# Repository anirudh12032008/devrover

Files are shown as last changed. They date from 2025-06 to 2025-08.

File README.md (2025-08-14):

# Dev Rover by Anirudh

Dev Rover is your personal rover which can move on its own, it has a esp32 with a camera that helps it to idetify things and navigate through the surroundings. it can be controlled by voice commands ( with the help me MAX9814) and can be controlleed by its own web applivation. It also has a speaker which can play some cool sounds. Its also equipped with a tilted 1.3 inc Oled display which can help the developer to see and visualize things. It ill run on 3/6 LiPo battery. It has 4 dc motors controlled by L298N motor driver. It has a 3D printed body which is light weight and durable. It can be used for various purposes like surveillance, exploration, and off course to show off to your friends.

## Why build dev rover?
I always wanted to build a robot like rover, which can move on my voice commands and off course I wanted to show it off to my friends. It will also help me entertain, remind, help while im programming and studying, it can also entertain me with some cool sounds when Im bored. and remind me to drink water and take breakes

## Features
- **Voice Control**: MAX9814 microphone.
- **Camera Navigation**: ESP32 camera for real-time video streaming and object identification.
- **Web Application Control**: Control the rover through web interface.
- **Audio Feedback**: Play sounds through a speaker for alerts and update
- **OLED Display**: 1.3-inch display for feedback and information.
- **Battery Powered**: Runs on a 3/6 LiPo battery 
- **4 DC Motors**: Powered by an L298N motor driver
- **3D Printed Body**: Lightweight and durable design

d1
d2
d3
d4

f4
circuit
p2
p1

f3
f2
f1

# final build
dev

# Youtube Link
https://youtu.be/ks2maEaWWV4?si=1bKzCrpTWsTYReYF

## Bill of Materials
| Component | Price (INR) | Price (USD) |
|---|---|---|
| ESP32 WROOM | 320 | 3.70 |
| TT DC Motor | 308 | 3.56 |
| Battery 3.7V (3-Pack of 2) | 546 | 6.30 |
| ESP32 Camera | 1040 | 12.01 |
| Battery Holder (2x3 cell) | 58 | 0.67 |
| L298D Motor Driver | 78 | 0.90 |
| TP4056 USB-C Charging Module | 32 | 0.37 |
| Switches | 202 | 2.33 |
| SH1106 OLED Display | 220 | 2.54 |
| SD Card Reader | 25 | 0.29 |
| MAX9814 Microphone Module | 166 | 1.92 |
| Speaker 2W 4Ω | 290 | 3.35 |
| PAM8403 Amplifier Module | 51 | 0.59 |
| 10-Segment LED Bar Graph | 70 | 0.81 |
| Buck Converter | 35 | 0.40 |
| WS2812 RGBIC LED Strip | 289 | 3.34 |
| M3 Screws (Pack of 10) | 120 | 1.39 |
| Terminal Block | 48 | 0.55 |
| 3D Case | 870 | 10.00 |
| PCB | 870 | 10.00 |
| Miscellaneous | 435 | 5.00 |
| **Tax** | **296.5** | **3.41** |
| | | |
| **Total** | **₹6369.5** | **$73.42**  |

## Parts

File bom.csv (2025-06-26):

Name | Price(INR) | Price(USD) | Link
ESP32 WROOM | 320 | 3.695150115 | https://ebhoot.in/shop-2/esp-wifi-boards/esp32-development-board-type-c-usb-ch340c-wifi-bluetooth-ultra-low-power-dual-core/
TT DC Motor | 308 | 3.556581986 | https://www.amazon.in/gp/product/B078NYD1MZ/ref=ewc_pr_img_1?smid=AJ6SIZC8YQDZX&psc=1
Battery 3.7V (3xPack of 2) | 546 | 6.304849885 | https://www.importdukan.com/li-ion-18650-3.7v-2600mah-battery-3c?search=battery+3.7
ESP32 Camera | 1040 | 12.00923788 | https://www.amazon.in/ESP32-Module-Bluetooth-OV2640-Camera/dp/B0BRXKNLFG/ref=sr_1_9?sr=8-9
Battery Holder (2x3 cell) | 58 | 0.6697459584 | https://ebhoot.in/shop-2/power-supply/battery-battery-holder/18650-battery-holder-for-lithium-ion-3-cell/
L298D Motor Driver | 78 | 0.9006928406 | https://ebhoot.in/shop-2/electronics-modules/motor-driver-modules/l298-2a-dual-motor-driver-module-with-pwm-control/
TP4056 USB-C Charging Module (x2) | 32 | 0.3695150115 | https://ebhoot.in/shop-2/electronics-modules/bms-module-battery-charging-module/tp4056-1a-li-ion-lithium-battery-charging-module-with-current-protection-type-c/
Switches | 202 | 2.33256351 | https://www.amazon.in/Electronicspices-Switchs-electronic-science-project/dp/B08TRDX6LW?s=industrial
SH1106 Oled | 220 | 2.540415704 | https://ebhoot.in/shop-2/display-devices/1-3-inch-i2c-iic-4-pin-oled-display-module-with-vcc-gnd-blue/
SD card reader | 25 | 0.2886836028 | https://ebhoot.in/shop-2/electronics-modules/interfacing-modules/micro-sd-card-module-breakout-board/
MAX9814 Microphone Module | 166 | 1.916859122 | https://www.importdukan.com/max9814-high-performance-microphone-agc-amplifier-module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
Speaker 2W 4ohm | 290 | 3.348729792 | https://www.amazon.in/Invento-8944638610755-Loudspeaker-Speaker-Replace/dp/B06XFJGV9K
PAM8403 | 51 | 0.5889145497 | https://www.importdukan.com/pam8403-mini-5v-digital-amplifier-board-with-switch-potentiometer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
10 Segment LED Bar Graph | 70 | 0.8083140878 | https://www.amazon.in/cart/smart-wagon?newItems=3d17a9ca-eada-479b-af5a-62ccfd44ab0d,1
Buck Convertor (x2) | 35 | 0.4041570439 | https://ebhoot.in/shop-2/electronics-modules/buck-boost-converters/lm2596-dc-dc-buck-converter-adjustable-step-down-power-supply-module/
WS2812 RGBIC LED Strip | 289 | 3.337182448 | https://www.amazon.in/AURECIS-Individually-Addressable-Non-Waterproof-Combinations/dp/B0F9FRZH69
M3 Screw( pack of 10) | 120 | 1.385681293 | https://www.amazon.in/Rpi-shop-Phillip-Phillips-Quantity/dp/B08FG7DL3T?sp_csd=d2lkZ2V0TmFtZT1zcF9hdGY
Terminal Block | 48 | 0.5542725173 | https://www.importdukan.com/2-pin-5.08mm-pitch-pluggable-screw-terminal-block-connector-blue
3D Case | 870 | 10 | printing legion
Tax | 296.5 | 3.408045977
PCB | 870 | 10 | Rough Estimate
Misc. | 435 | 5
 |  | 0
 |  | 0
Total | 6369.5 | 73.41959332

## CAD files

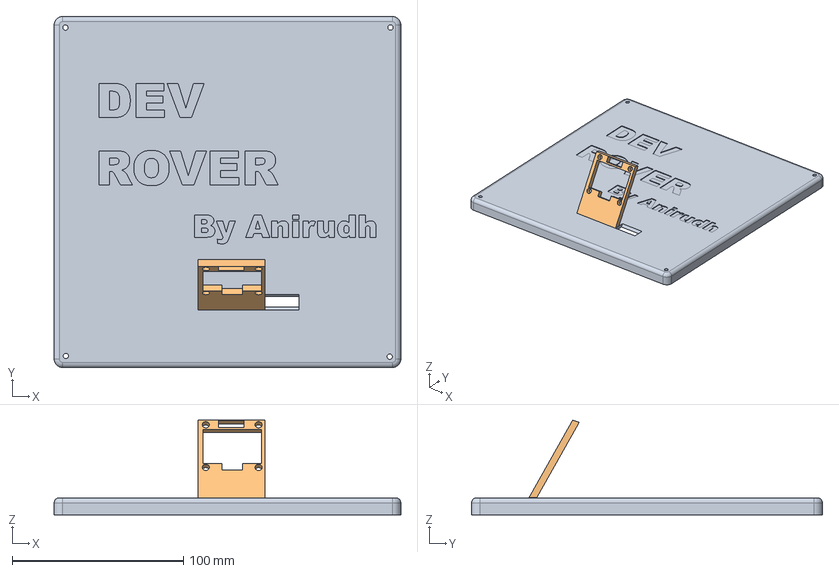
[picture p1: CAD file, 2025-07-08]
cad/top_rover.step
202.5 x 205.0 x 55.4 mm

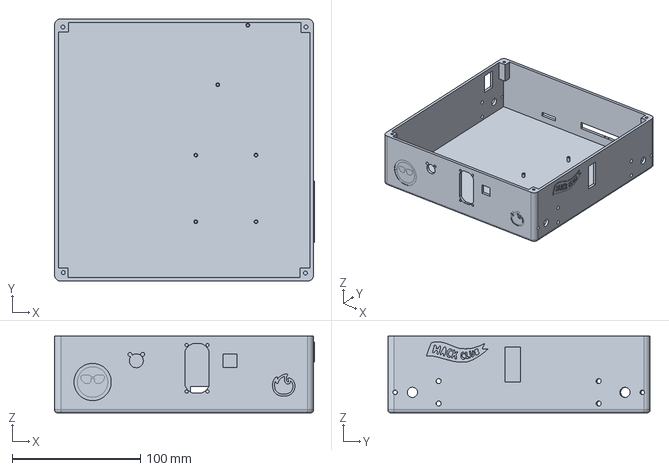
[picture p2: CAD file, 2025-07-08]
cad/Bottom_rover.step
203.1 x 205.0 x 60.0 mm

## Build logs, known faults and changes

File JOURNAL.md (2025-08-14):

# JOURNAL 
Title - " DEV ROVER "
Author - Anirudh Sahu
description - Dev Rover is your personal rover which can move on its own, it has a esp32 with a camera that helps it to idetify things and navigate through the surroundings. it can be controlled by voice commands ( with the help me MAX9814) and can be controlleed by its own web applivation. It also has a speaker which can play some cool sounds. Its also equipped with a tilted 1.3 inc Oled display which can help the developer to see and visualize things. It ill run on 3/6 LiPo battery. It has 4 dc motors controlled by L298N motor driver. It has a 3D printed body which is light weight and durable. It can be used for various purposes like surveillance, exploration, and off course to show off to your friends.
created_at - 2025-06-11
## Total Time - 44 Hr

## June 11th: researched around the topic and created a rough schematic and PCB
3 PM IST - 6:20 PM IST
Initially I started with creating a rough plan of what exactly to include in my project.
As its a smart rover ill need a few dc motor a couple of servo motors and a mini computer to make it smart.
So as this is my starting project I didnt really knew how to get started with the PCB designing. i used Easy EDA but still when I seareched for components There were wayy tooo many options so I was overwhelmed and confused then I selected a esp32 and a L298N I have a knowledge of physical components just the firmware is new then I made the intial connections with the esp32 but later I found that the ESP32 I was using didnt had a 5V power supply so I had to restart and find a new one which took a bit time and also I had to understand why this happened. next I created a rough pcb and a 3d view of it I'm now planning to try some other alternatives for the designing part. 



Total time spend 3 hr

## June 12th: Started with designing the case
6 pm ist to 10 pm ist
These were one of the worst hours in my journey. I started with the recommendations from others to use onshape but when I actually started I had a really hard time. first the models I imported had 300 parts so to move it to the center I had to select all which made my computer burst lol ( not literally ) then I learned about onshape it had very less tutorials also so still I managed but then again it started to lag too much. I literally couldnt think of anything else then I asked in slack so I'll start my journey with most probable fusion360 from tommorow. Todays day made me learn many things and I also have models of esp32, servo motor, dc motor, l298 motor Driver

 
Total time spend : 4 hr

## Jun 13: Continue Designing the case
4 PM IST to 7:45 PM IST
So I started with downloading Fusion 360, Its definitely better then Onshape, so I knew what exactly I wanted to get started on took some time to get familier to the software then got started with the actual work, imported to models took some more time then started to create a sketch and then a plane then a surface and excruded it to make a base. wwasnt sure with the dimensions so researched online to find the right dimensions. ill continue tomorrow with the case and planning to move to the electriv circuits next

Total time spend : 3.75 Hr

## Jun 14: Continue with the planning and the 3D case
6:30 PM IST to 11:30 PM IST
Continued developing the model. Had some issue regarding how would the actual model look like but after exploring other ideas and designs I planned to make it in like a Box thats like a perfect robo shape lol, so I first researched for the components that ill be using and found there 3d models to import, due to budget constraint I droppeed the servo motors for the pickup thing. But I added the the mother components. Created the sketches for each model and had my case in 2 parts for top and bottom also added the screen. Took some time to seaerch online on how to do a thing but now I am familiar with the overall software so from today things will go on more fast!!! 





Total Time Spend : 4 Hr

## June 15: Changed the components and layout
7:15 PM IST to 11 PM IST
So today I continued with the case but then after reconsideration I reselected the components required, I replaced the 0.93 inch oled with 1.3 one and added other components like a speaker and a microphone to receive audio input and I also changed the overall layout so I removed the previous bodies and components and added the new also this time I kept in mind about where exactly each component will be in the final design. Now I have included all the models that I will be using in the final rover. I made sure that the 3D model that I was using is available on Amazon or other places and have the right dimensions so that I don't face any issue later. Some models weren't available on grabcad so I surfed the web for it. 




Total Time Spend: 3.75 Hr

## June 16: Designed the 3d structure especially for oled
I started with creating the base structure. firstly created the sketches for all components.then I worked for the oled display structure. It took a bit time but atleast I can see things turning into the model. Tommorow I'll try to complete the structure for all of the components.





Total time Spent: 3hr

## June 17: Designed most of the model
Continuing the work that I did yesterday, took a bit long because first my sketch pallete disappeared asked for help but didnt found any solution both on internet and slack. Still I continued with the designing first I finished the bottom then insted of procastination I finished all sides also and added holes where ever needed, added a few holes on the base for esp and l298




Total Time Spent: 4.5 Hr

## June 19: Completed the 3D model
Finished completing the 3D model, added the holes and improved some small details by taking feedbacks on slack. I will be using rgb strip around it so left a small hole near the oled stand to let the wires in


Total Time Spent: 2 Hr

## June 20: Finished the Case and created the BOM 
added a hole for the Camera, while creating the BOM I also noticed that the esp32 was having wrong holes so fixed it also improved the holes and fixed minor issues on the suggestions from others. Creating the BOM was the most important part, for India i couldn't find any website which had all the parts so at last i used Amazon. then the issue was there were many parts which had shipping cost more then the actual part cost. some had the minimum order quantity requirements. But Overall I got everything in 80-85$ which is quite good as of what I had thought initially.
Time Spent : 3 Hr

## June 21: Completed the code for the rover to move 
Added a web server for the rover to communicate with and implemented the logics to move
r1
Time Spent : 2.5 Hr

## June 22: Completed the full Project
Implemented all the features in the code so that I have full code available when then hardware arrives, added the remaining parts. Researched about some small details that I could improve in the overall project.
Written the Readme for the Project. Added some cool details in the 3D model. Created the Circuit diagram
f7
f6
f5
circuit
f4
f3
f2
f1

Time Spent - 6Hr ( including 1AM 23th)

## June 25: Created PCB
As Cyao told me to create a PCB I started creating the PCB, making it a big pcb would just increase its price so I tried to keep it compact. I initally started with creating my own motor driver but then when I checked the price for PCBA it was more then 5x a module so I decided to use only hand soldered items to save money on the PCB and create the pcb to make things clutter free.
p2
p1
Time Spent - 3.5 hr

## July 9-10: Started building physically 
recived all the parts so I started to build the main project. couldn't get the 3d print so I planned to work on a wooden base for prototype. integrated the camera and also completed the working rover. it can move right now the main issue was that Arduino IDE sucks adn the esp32 am was getting too hot
Screenshot_2025-07-11-08-56-51-107_com android chrome
Screenshot_2025-07-11-08-57-54-085_com gallery player
Screenshot_2025-07-11-08-58-22-102_com gallery player


## Day 12 
So now I added the PAM amplifier and speaker but the issue was I couldn't play anything so then  headed to
Install the sd card module with it I did everything but still it was not working
Then I thought maybe it's some issue with my SD Card so I tried 3 more cards and formatted them and tried again but still it wasn't working but then U realised that how fool I am I was powering it with 3.3V when it should have been powered by 5V after doing that yess it started working
So I setup that and yeah the audio system was working but was having very very very bad quality but I found some more code online to take reference and then after some long tine taking compiling I made something working, I haven't been able to get a perfect audio but it is pretty good quality now
photo_6102760546496530531_w
photo_6102760546496530527_w
time - 7hr

## Day 13
Added the camera to the main esp32. I streammed the espcam on its own server and then used it with the main Esp32 I also added a new endpoint to control the flash value then I changed the main Esp32 code to connect with the espcam server and show the data I also added slider so that I can control the led but then I realised I should also add some way to control the quality so I added another slider to control the quality of the feed. Now the main issue coming is that the espcam is shutting down after like 1-2 minutes!
So, today I solved the ESP32 camera problem by finding a capacitor as I didn't have a capacitor in my BOM, but I really needed it. So I went to a shop and I asked ChatGPT which one to get. So he suggested me to get a 470 MUF or 1000 MUF. So, I went there and I preferred 1000 MUF because the bigger it is, the better it is. Like in the value-wise and it's a pretty big one. Around 35 volts, so yeah. After using that and I also got a 470 MUF for the main ESP32 also. Because it told me that it would avoid the voltage spikes. Still the esp cam had the same issue
So, still it wasn't working, so I need to diagnose the main issue. To be honest, I couldn't find anything which was doing it. So I went to the internet, I searched for a few things, and then I got a Reddit thread that some user faced the same issue but with some other module, because I was fool, I was covering it with the L298 motor driver's 5V, which is 2-2 unstable. Because whenever the car moves, the voltage drops, and the ESP cam is like a current sucker, so it do need a lot of current, I guess around 500 or 600 ampere. So yeah, I used a buck converter to drop the voltage from the 3 battery pack from 12V to 5V, and used it for the power supply, and it works pretty well now.

photo_6102760546496530523_w

time - 8hr

## Day 14
So now I got into another trouble that the camera and the main ESP shut down like whenever the motor started running. So it was pretty strange because yesterday it was working pretty fine. So I did some recompiling and some more testing. Externally I tested it but everything was working so I didn't know what issue came. So then I took out my voltmeter and multimeter and then when I placed it on the battery pack I came to know that the batteries are discharged. It's not 12V now it's around 7V due to which the L298 drives too much power and the ESP just shut down. So I had another issue that how would I charge the batteries. So I had no option to actually charge the batteries as I got a TP4056 but it was a 3S battery pack. So how would I even charge it. So this was a design flaw from my side. And I searched online for some of the things that could do the job but I couldn't find anything. So what I did is I just had a couple of TP4056 from the local store and some battery holders. And I have a lot of chargers at my home so I just plugged every 3 battery cell into different battery holders and charged them individually. And after that it was working really great. So yeah that was a really nightmare situation.
photo_6102760546496530516_w
time - 2hr

## Day 15
So, today I received my PCB and when I saw the PCB, the obvious flaw that I came to notice is that I was having the wrong MCU. I was having the ESP32 with 30 pins but in the PCB it was of 38 pins and I was really screwed up because I couldn't really return it as I just opened packet of ESP32. So, yeah, I was in a really doubtful situation but I had only one choice. I first searched the internet to find any relevant resources but I couldn't find any. So, my next attempt was to manually fix this design flaw.
photo_6102760546496530536_w
time - 3hr

## Day 16 
I added everything that was left added the rgb strip, the led graph, added the eyes to the oled this was really tough because of obvious reasons that it was for that shitty 0.96 oled all the libraries so I needed to make my own for the 1.3 so It was really exhaustive learning about stuff asking gemini but finally I managed to get it done
I also improved the overall UI of the web interfce because it was pretty shitty before 
photo_6102760546496530561_w
photo_6102760546496530560_w
photo_6102760546496530559_w

time - 4hr

## Day 17
So I started doing the final build and I;m really really tired now  it was very messy everything started to stop working and then start working so I knew I am fucked up but I dont really have words for what happened it just did happened but somehow I did it and im dead now lol
photo_6120626171633846730_w
photo_6120626171633846731_w
photo_6120626171633846732_w
photo_6120626171633846733_w
photo_6120626171633846734_w
dev

time - 3hr

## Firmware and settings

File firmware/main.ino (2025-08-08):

#include <WiFi.h>
#include <AsyncTCP.h>
#include <ESPAsyncWebServer.h>
#include <SD.h>
#include <SPI.h>
#include <U8g2lib.h>
#include <Wire.h>
#include <Adafruit_NeoPixel.h>

// Use a different GPIO pin since 23 is for the SD card
#define LED_PIN    2 // Data pin for the NeoPixel strip
#define NUM_LEDS   60 // Number of LEDs in your 1-meter strip

Adafruit_NeoPixel strip(NUM_LEDS, LED_PIN, NEO_GRB + NEO_KHZ800);

File audioFile;
bool isPlaying = false;
#define SD_CS 5

// ====== WiFi Config ======
const char* ssid = "Dev Bhai OP";
const char* password = "devbhai123omsairam";
const char* ap_ssid = "ESP32-Rover-AP";
const char* ap_password = "robotpassword";
// ====== Motor Pins ======
const int IN1 = 26, IN2 = 27, IN3 = 14, IN4 = 12, ENA = 13, ENB = 33;

// ====== Speaker & Mic Config ======
const int speakerPin = 25;  // DAC1 -> PAM8403
const int micPin = 34;
int threshold = 1940;
unsigned long lastTriggerTime = 0;
unsigned long debounceDelay = 100;
int micValue = 0;
bool soundDetected = false;

#define SCREEN_WIDTH 128
#define SCREEN_HEIGHT 64
#define OLED_RESET -1
#define SCREEN_ADDRESS 0x3C

U8G2_SH1106_128X64_NONAME_F_HW_I2C u8g2(U8G2_R0, /* reset=*/ U8X8_PIN_NONE);

// ====== Globals ======
int currentSpeed = 150;
String currentDir = "stop";
AsyncWebServer server(80);

// Eye state variables (simplified)
int left_eye_x_pos = 0;
int left_eye_y_pos = 0;
int right_eye_x_pos = 0;
int right_eye_y_pos = 0;
const int eye_size = 40;
const int eye_spacing = 10;
const int corner_radius = 10;
const int eye_offset = 10; // Offset for movements



void draw_eyes() {
  u8g2.clearBuffer();
  u8g2.drawRBox(left_eye_x_pos, left_eye_y_pos, eye_size, eye_size, corner_radius);
  u8g2.drawRBox(right_eye_x_pos, right_eye_y_pos, eye_size, eye_size, corner_radius);
  u8g2.sendBuffer();
}

void center_eyes() {
  left_eye_x_pos = (SCREEN_WIDTH - (eye_size * 2 + eye_spacing)) / 2;
  left_eye_y_pos = (SCREEN_HEIGHT - eye_size) / 2;
  right_eye_x_pos = left_eye_x_pos + eye_size + eye_spacing;
  right_eye_y_pos = left_eye_y_pos;
  draw_eyes();
}

// ====== Tone Functions (unchanged) ======
void smoothBeep(int freq, int durationMs) {
  const int samplesPerCycle = 30;
  float step = 2 * 3.14159 / samplesPerCycle;
  unsigned long endTime = millis() + durationMs;
  while (millis() < endTime) {
    for (int i = 0; i < samplesPerCycle; i++) {
      float wave = sin(i * step);
      int val = 128 + int(wave * 100);
      dacWrite(speakerPin, val);
      delayMicroseconds(1000000 / (freq * samplesPerCycle));
    }
  }
}

void gap(int ms = 100) {
  dacWrite(speakerPin, 0);
  delay(ms);
}

void sayHello() {
  smoothBeep(500, 120); gap(80);
  smoothBeep(460, 100); gap(80);
  smoothBeep(420, 100); gap(80);
  smoothBeep(600, 150); gap(200);
}

void sayWorld() {
  smoothBeep(300, 120); gap(60);
  smoothBeep(360, 100); gap(60);
  smoothBeep(400, 100); gap(60);
  smoothBeep(440, 100); gap(60);
  smoothBeep(480, 120); gap(200);
}

void playWav(const char* filename) {
  if (isPlaying) return;
  audioFile = SD.open(filename);
  if (!audioFile) {
    Serial.println("❌ Cannot open WAV file!");
    return;
  }
  isPlaying = true;
  uint8_t buffer[1];
  for (int i = 0; i < 44; i++) audioFile.read();
  while (audioFile.available() && isPlaying) {
    audioFile.read(buffer, 1);
    dacWrite(speakerPin, buffer[0]);
    delayMicroseconds(125);
  }
  audioFile.close();
  isPlaying = false;
  dacWrite(speakerPin, 0);
}

void stopPlayback() {
  if (isPlaying) {
    isPlaying = false;
    if (audioFile) audioFile.close();
    dacWrite(speakerPin, 0);
  }
}

// ====== Motor Movement and Eye Control ======
void moveCar(String dir, int speed) {
  currentDir = dir;
  currentSpeed = map(speed, 0, 100, 0, 255);

  digitalWrite(IN1, dir == "forward" || dir == "right");
  digitalWrite(IN2, dir == "backward" || dir == "left");
  digitalWrite(IN3, dir == "forward" || dir == "left");
  digitalWrite(IN4, dir == "backward" || dir == "right");

  if (dir == "stop") {
    digitalWrite(IN1, LOW); digitalWrite(IN2, LOW);
    digitalWrite(IN3, LOW); digitalWrite(IN4, LOW);
    center_eyes();
  } else if (dir == "forward") {
    center_eyes();
  } else if (dir == "backward") {
    int centerX = (SCREEN_WIDTH - (eye_size * 2 + eye_spacing)) / 2;
    int centerY = (SCREEN_HEIGHT - eye_size) / 2;
    left_eye_x_pos = centerX;
    left_eye_y_pos = centerY + eye_offset;
    right_eye_x_pos = centerX + eye_size + eye_spacing;
    right_eye_y_pos = centerY + eye_offset;
    draw_eyes();
  } else if (dir == "left") {
    int centerX = (SCREEN_WIDTH - (eye_size * 2 + eye_spacing)) / 2;
    int centerY = (SCREEN_HEIGHT - eye_size) / 2;
    left_eye_x_pos = centerX - eye_offset;
    left_eye_y_pos = centerY;
    right_eye_x_pos = centerX + eye_size + eye_spacing - eye_offset;
    right_eye_y_pos = centerY;
    draw_eyes();
  } else if (dir == "right") {
    int centerX = (SCREEN_WIDTH - (eye_size * 2 + eye_spacing)) / 2;
    int centerY = (SCREEN_HEIGHT - eye_size) / 2;
    left_eye_x_pos = centerX + eye_offset;
    left_eye_y_pos = centerY;
    right_eye_x_pos = centerX + eye_size + eye_spacing + eye_offset;
    right_eye_y_pos = centerY;
    draw_eyes();
  }

  analogWrite(ENA, currentSpeed);
  analogWrite(ENB, currentSpeed);
}

void setupAP() {
  Serial.println("❌ WiFi failed, starting Access Point.");
  WiFi.softAP(ap_ssid, ap_password);
  IPAddress apIP = WiFi.softAPIP();
  Serial.print("✅ AP IP address: ");
  Serial.println(apIP);

  // You may want to display this info on the OLED
  // u8g2.clearBuffer();
  // u8g2.setFont(u8g2_font_6x10_tf);
  // u8g2.drawStr(0, 10, "AP Mode Active");
  // u8g2.drawStr(0, 25, "SSID:");
  // u8g2.drawStr(40, 25, ap_ssid);
  // u8g2.drawStr(0, 40, "Password:");
  // u8g2.drawStr(60, 40, ap_password);
  // u8g2.sendBuffer();
}

void setup() {
  Serial.begin(115200);
  pinMode(IN1, OUTPUT); pinMode(IN2, OUTPUT);
  pinMode(IN3, OUTPUT); pinMode(IN4, OUTPUT);
  pinMode(ENA, OUTPUT); pinMode(ENB, OUTPUT);
  dacWrite(speakerPin, 0);

  u8g2.begin();
  u8g2.setDrawColor(1);
  center_eyes();
  strip.begin();
  strip.show();

  // ====== Wi-Fi Connection Logic with Fallback ======
  Serial.print("Connecting to WiFi...");
  WiFi.begin(ssid, password);

  unsigned long wifiConnectStartTime = millis();
  while (WiFi.status() != WL_CONNECTED && millis() - wifiConnectStartTime < 10000) { // 10 second timeout
    delay(500);
    Serial.print(".");
    center_eyes(); // Animate eyes while trying to connect
  }

  if (WiFi.status() == WL_CONNECTED) {
    Serial.println("\n✅ WiFi Connected!");
    Serial.print("IP Address: ");
    Serial.println(WiFi.localIP());
  } else {
    setupAP(); // Fallback to Access Point if connection fails
  }

  // ... (rest of your setup code remains the same)
  SPI.begin(18, 19, 23, SD_CS);
  if (!SD.begin(SD_CS, SPI)) {
    Serial.println("❌ SD card failed!");
  } else {
    Serial.println("✅ SD card initialized!");
  }

  server.on("/control", HTTP_GET, [](AsyncWebServerRequest *request){
    String dir = request->getParam("dir")->value();
    int speed = request->getParam("speed")->value().toInt();
    moveCar(dir, speed);
    request->send(200, "text/plain", "OK");
  });

  server.on("/say", HTTP_GET, [](AsyncWebServerRequest *request){
    String word = request->getParam("word")->value();
    if (word == "hello") sayHello();
    else if (word == "world") sayWorld();
    else if (word == "startup") { sayHello(); sayWorld(); }
    request->send(200, "text/plain", "Sound Played");
  });

  server.on("/play", HTTP_GET, [](AsyncWebServerRequest *request) {
    if (request->hasParam("track")) {
      String name = request->getParam("track")->value();
      if (name == "test1") playWav("/test1.wav");
      else if (name == "test2") playWav("/test2.wav");
      request->send(200, "text/plain", "Playing " + name);
    } else {
      request->send(400, "text/plain", "No track specified");
    }
  });

  server.on("/stop", HTTP_GET, [](AsyncWebServerRequest *request) {
    stopPlayback();
    request->send(200, "text/plain", "Stopped");
  });

  server.on("/mic", HTTP_GET, [](AsyncWebServerRequest *request){
    String json = "{\"value\":" + String(micValue) + ",\"status\":\"" +
                  (soundDetected ? "Sound Detected!" : "Silent") + "\"}";
    request->send(200, "application/json", json);
  });

  server.on("/", HTTP_GET, [](AsyncWebServerRequest *request){
    String html = R"rawliteral(
<!DOCTYPE html>
<html lang="en">
<head>
    <meta charset="UTF-8">
    <meta name="viewport" content="width=device-width, initial-scale=1.0">
    <title>Dev Rover Control</title>
    <style>
        /* A slightly modified version of Tailwind CSS for a dark theme */
        body {
            font-family: ui-sans-serif, system-ui, -apple-system, BlinkMacSystemFont, "Segoe UI", Roboto, "Helvetica Neue", Arial, "Noto Sans", sans-serif;
            background-color: #1a202c; /* dark gray */
            color: #e2e8f0; /* light gray */
            padding: 1rem;
        }
        h1 {
            color: #ecc94b; /* yellow */
            font-size: 1.875rem; /* 30px */
            line-height: 2.25rem; /* 36px */
            text-align: center;
            margin-bottom: 2rem;
        }
        h2 {
            font-size: 1.5rem; /* 24px */
            line-height: 2rem; /* 32px */
            margin-top: 1.5rem;
            margin-bottom: 0.5rem;
            color: #a0aec0;
            text-align: center;
        }
        .container {
            max-width: 42rem; /* 672px */
            margin-left: auto;
            margin-right: auto;
            display: flex;
            flex-direction: column;
            gap: 1.5rem;
        }
        .grid {
            display: grid;
            grid-template-columns: repeat(2, minmax(0, 1fr));
            gap: 0.5rem;
        }
        .grid-full {
            display: grid;
            grid-template-columns: 1fr;
            gap: 0.5rem;
        }
        @media (min-width: 640px) {
            .grid {
                grid-template-columns: repeat(3, minmax(0, 1fr));
            }
        }
        button {
            display: flex;
            justify-content: center;
            align-items: center;
            padding: 1rem 1.25rem;
            border-radius: 0.5rem;
            font-weight: 600;
            font-size: 1rem;
            line-height: 1.5rem;
            color: #1a202c;
            background-color: #ecc94b;
            border: none;
            cursor: pointer;
            transition-property: background-color;
            transition-duration: 150ms;
        }
        button:active {
            background-color: #d69e2e; /* dark yellow on press */
        }
        .slider-container {
            width: 100%;
            display: flex;
            flex-direction: column;
            align-items: center;
            margin: 1rem 0;
            background-color: #2d3748;
            padding: 1rem;
            border-radius: 0.5rem;
        }
        .slider-container label {
            font-size: 1rem;
            line-height: 1.5rem;
            margin-bottom: 0.5rem;
        }
        .slider-container input[type="range"] {
            width: 90%;
            -webkit-appearance: none;
            height: 0.5rem;
            border-radius: 9999px;
            background: #4a5568;
            outline: none;
            transition: opacity 0.2s;
        }
        .slider-container input[type="range"]::-webkit-slider-thumb {
            -webkit-appearance: none;
            appearance: none;
            width: 1.25rem;
            height: 1.25rem;
            border-radius: 9999px;
            background: #ecc94b;
            cursor: pointer;
        }
        .mic-box {
            background-color: #2d3748; /* gray */
            padding: 1rem;
            border-radius: 0.5rem;
            margin-top: 1rem;
        }
        .mic-box p {
            margin: 0;
            font-size: 1rem;
            line-height: 1.5rem;
            text-align: left;
        }
        .mic-box .status-text {
            color: #68d391; /* green */
        }
    </style>
</head>
<body>
    <div class="container">
        <h1>🚗 Dev Rover Control</h1>
        
        <h2>📷 Live Camera</h2>
        <img src="http://192.168.29.222:81/stream" style="width:100%; border-radius:10px; margin-bottom:10px;">
        
        <div class="slider-container">
            <label for="flashSlider">Flash Brightness: <span id="flashVal">0</span></label>
            <input type="range" min="0" max="255" value="0" id="flashSlider" oninput="updateFlash(this.value)">
        </div>
        <div class="slider-container">
            <label for="resSlider">📷 Resolution: <span id="resLabel">Medium</span></label>
            <input type="range" id="resSlider" min="2" max="10" step="1" value="6" oninput="changeRes(this.value)">
        </div>
        
        <div class="grid">
            <button onmousedown="send('forward',100)" onmouseup="send('stop',0)" ontouchstart="send('forward',100)" ontouchend="send('stop',0)">Forward</button>
            <button onmousedown="send('backward',100)" onmouseup="send('stop',0)" ontouchstart="send('backward',100)" ontouchend="send('stop',0)">Backward</button>
            <button onmousedown="send('left',100)" onmouseup="send('stop',0)" ontouchstart="send('left',100)" ontouchend="send('stop',0)">Left</button>
            <button onmousedown="send('right',100)" onmouseup="send('stop',0)" ontouchstart="send('right',100)" ontouchend="send('stop',0)">Right</button>
            <button class="grid-full" onclick="send('stop',0)">Stop</button>
        </div>
        <div class="slider-container">
            <label for="spd">Speed: <span id="speedVal">50</span>%</label>
            <input type="range" min="0" max="100" value="50" id="spd" oninput="sendSpeed(this.value)">
        </div>
        <div class="grid">
            <button onclick="fetch('/play?track=test1')">▶️ Play test1.wav</button>
            <button onclick="fetch('/play?track=test2')">▶️ Play test2.wav</button>
            <button onclick="fetch('/stop')">⏹️ Stop</button>
        </div>
        <div class="mic-box">
            <h2>🎤 Mic Monitor</h2>
            <p>Value: <span id="micVal">---</span></p>
            <p>Status: <span id="micStatus" class="status-text">Loading...</span></p>
        </div>
    </div>
    <script>
        function updateFlash(val) {
            document.getElementById("flashVal").textContent = val;
            fetch("http://192.168.29.222/flash?level=" + val);
        }
        function changeRes(val) {
            const labels = {
                2: "Ultra High",
                3: "Very High",
                4: "High",
                6: "Medium",
                8: "Low",
                9: "Very Low",
                10: "Ultra Low"
            };
            document.getElementById("resLabel").textContent = labels[val] || "Custom";
            fetch("http://192.168.29.222/control?var=framesize&val=" + val).then(() => console.log("Resolution changed to", val));
        }
        let currentDir = 'stop';
        function send(dir, speed) {
            currentDir = dir;
            fetch(`/control?dir=${dir}&speed=${speed}`);
        }
        function sendSpeed(val) {
            document.getElementById("speedVal").textContent = val;
            fetch(`/control?dir=${currentDir}&speed=${val}`);
        }
        setInterval(() => {
            fetch('/mic')
                .then(res => res.json())
                .then(data => {
                    document.getElementById("micVal").textContent = data.value;
                    document.getElementById("micStatus").textContent = data.status;
                });
        }, 500);
    </script>
</body>
</html>
)rawliteral";
    request->send(200, "text/html", html);
  });

  server.begin();
  sayHello(); sayWorld();
}
uint8_t chase_color_index = 0; // 0-255, for the color wheel

void chase() {
  // Use a static variable to keep track of the chasing segment's starting point
  static int i = 0;
  
  // Update the color index for the next animation frame
  chase_color_index++;
  
  // Clear the entire strip to black before drawing the next frame
  strip.clear();
  
  // Set the color for the 30-LED chasing segment
  for(int k = 0; k < 45; k++) {
    // The Wheel() function maps a 0-255 value to a color on the RGB spectrum
    strip.setPixelColor((i + k) % NUM_LEDS, strip.ColorHSV( (chase_color_index * 256 / 30) + (k * 256 / 30) ) );
  }

  // Update strip and move the starting point
  strip.show();
  i = (i + 1) % NUM_LEDS; // Move the starting LED of the chase
  delay(30); // Adjust this value to change the speed of the chase
}

void loop() {
  micValue = analogRead(micPin);
  soundDetected = (micValue > threshold && millis() - lastTriggerTime > debounceDelay);
  if (soundDetected) lastTriggerTime = millis();

  chase(); // Green

}

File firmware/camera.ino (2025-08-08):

#include "esp_camera.h"
#include <WiFi.h>

// ===========================
// Select camera model in board_config.h
// ===========================
#include "board_config.h"

// ===========================
// Enter your WiFi credentials
// ===========================
const char *ssid = "Dev Bhai OP";
const char *password = "devbhai123omsairam";

void startCameraServer();
void setupLedFlash();

void setup() {
  Serial.begin(115200);
  Serial.setDebugOutput(true);
  Serial.println();

  camera_config_t config;
  config.ledc_channel = LEDC_CHANNEL_0;
  config.ledc_timer = LEDC_TIMER_0;
  config.pin_d0 = Y2_GPIO_NUM;
  config.pin_d1 = Y3_GPIO_NUM;
  config.pin_d2 = Y4_GPIO_NUM;
  config.pin_d3 = Y5_GPIO_NUM;
  config.pin_d4 = Y6_GPIO_NUM;
  config.pin_d5 = Y7_GPIO_NUM;
  config.pin_d6 = Y8_GPIO_NUM;
  config.pin_d7 = Y9_GPIO_NUM;
  config.pin_xclk = XCLK_GPIO_NUM;
  config.pin_pclk = PCLK_GPIO_NUM;
  config.pin_vsync = VSYNC_GPIO_NUM;
  config.pin_href = HREF_GPIO_NUM;
  config.pin_sccb_sda = SIOD_GPIO_NUM;
  config.pin_sccb_scl = SIOC_GPIO_NUM;
  config.pin_pwdn = PWDN_GPIO_NUM;
  config.pin_reset = RESET_GPIO_NUM;
  config.xclk_freq_hz = 20000000;
  config.frame_size = FRAMESIZE_UXGA;
  config.pixel_format = PIXFORMAT_JPEG;  // for streaming
  //config.pixel_format = PIXFORMAT_RGB565; // for face detection/recognition
  config.grab_mode = CAMERA_GRAB_WHEN_EMPTY;
  config.fb_location = CAMERA_FB_IN_PSRAM;
  config.jpeg_quality = 12;
  config.fb_count = 1;

  // if PSRAM IC present, init with UXGA resolution and higher JPEG quality
  //                      for larger pre-allocated frame buffer.
  if (config.pixel_format == PIXFORMAT_JPEG) {
    config.frame_size = FRAMESIZE_SVGA;
    config.fb_location = CAMERA_FB_IN_DRAM;
  } else {
    // Best option for face detection/recognition
    config.frame_size = FRAMESIZE_240X240;
#if CONFIG_IDF_TARGET_ESP32S3
    config.fb_count = 2;
#endif
  }

#if defined(CAMERA_MODEL_ESP_EYE)
  pinMode(13, INPUT_PULLUP);
  pinMode(14, INPUT_PULLUP);
#endif

  // camera init
  esp_err_t err = esp_camera_init(&config);
  if (err != ESP_OK) {
    Serial.printf("Camera init failed with error 0x%x", err);
    return;
  }

  sensor_t *s = esp_camera_sensor_get();
  // initial sensors are flipped vertically and colors are a bit saturated
  if (s->id.PID == OV3660_PID) {
    s->set_vflip(s, 1);        // flip it back
    s->set_brightness(s, 1);   // up the brightness just a bit
    s->set_saturation(s, -2);  // lower the saturation
  }
  // drop down frame size for higher initial frame rate
  if (config.pixel_format == PIXFORMAT_JPEG) {
    s->set_framesize(s, FRAMESIZE_QVGA);
  }

#if defined(CAMERA_MODEL_M5STACK_WIDE) || defined(CAMERA_MODEL_M5STACK_ESP32CAM)
  s->set_vflip(s, 1);
  s->set_hmirror(s, 1);
#endif

#if defined(CAMERA_MODEL_ESP32S3_EYE)
  s->set_vflip(s, 1);
#endif

// Setup LED FLash if LED pin is defined in camera_pins.h
#if defined(LED_GPIO_NUM)
  setupLedFlash();
#endif

 IPAddress local_IP(192, 168, 29, 222);
IPAddress gateway(192, 168, 29, 1);
IPAddress subnet(255, 255, 255, 0);
IPAddress primaryDNS(8, 8, 8, 8);  // Optional
IPAddress secondaryDNS(1, 1, 1, 1);  // Optional

WiFi.config(local_IP, gateway, subnet, primaryDNS, secondaryDNS);
WiFi.begin(ssid, password);
WiFi.setSleep(false);


  Serial.print("WiFi connecting");
  while (WiFi.status() != WL_CONNECTED) {
    delay(500);
    Serial.print(".");
  }
  Serial.println("");
  Serial.println("WiFi connected");

  startCameraServer();

  Serial.print("Camera Ready! Use 'http://");
  Serial.print(WiFi.localIP());
  Serial.println("' to connect");
}

void loop() {
  // Do nothing. Everything is done in another task by the web server
  delay(10000);
}

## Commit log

2025-06-20 Uploaded BOM
    [BOM.csv]
2025-06-22 Updated BOM
    [BOM.csv]
2025-06-25 added PCB
2025-06-25 Update bom
2025-06-26 Rename 3D Model devrover.rar to cad/3D Model devrover.rar
2025-06-26 Update and rename BOM.csv to bom/BOM.csv
    [BOM.csv]
2025-06-26 Update and rename BOM devrover.csv to bom/BOM devrover.csv
    [BOM devrover.csv]
2025-06-29 Update and rename bom/BOM devrover.csv to bom.csv
    [bom.csv]
